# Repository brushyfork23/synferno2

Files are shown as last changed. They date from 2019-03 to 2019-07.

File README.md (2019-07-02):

# Synferno

Synferno is a flame-effect synchronizer which allows a DJ to easily trigger complex sequences of fireballs which perfectly match the music they’re playing.  The system consists of a console and four flame effects.  This codebase contains designs for building the console, the software which runs on it, and a the software for a flame-effect simulator to allow for bench testing.

## Physical Layout

The face of the console has 16 interface components:

 * One key-lock switch to ensure user is permitted to run console
 * One arming switch to ensure user wants to run console
 * Five white illuminated push-buttons to select sequence
 * Four red illuminated push-buttons for manually firing each of the four output channels individually
 * One large red illuminated push-button for manually firing all four output channels at once
 * One yellow illuminated push-button for resetting the down-beat and for flashing at the first beat of each stanza
 * One yellow illuminated push-button for manually tapping out a BPM and for flashing on each beat
 * One OLED screen which displays a menu
 * One rotary-encoder with integrated push-button for selecting and changing menu options

The back of the console has seven interface components:

 * One IEC power socket
 * One DIN-5 MIDI input port
 * Four SpeakOn connectors to deliver activation power to the four flame effects
 * One rocker-style power switch

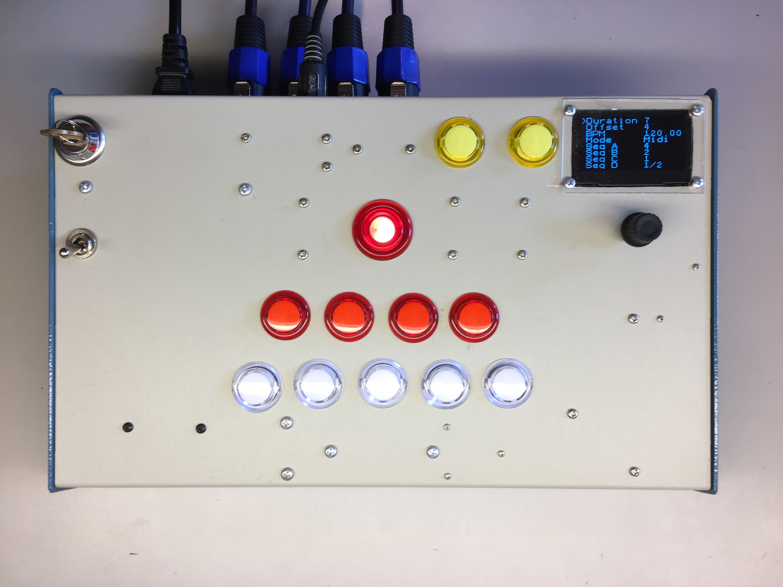
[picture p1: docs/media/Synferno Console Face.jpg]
Synferno Console Face


Included in `docs/diagrams/` are [renderings of each face and the positioning of internal components](docs/diagrams/Synferno2%20Console%20Interface%20Layout)

## Usage

The console’s primary function is to accept a BPM and energize the four SpeakOn output ports according to a selected sequence.  BPM can be read from a connected MIDI device or manually set by either tapping repeatedly on the Tap button or setting a value in the menu with the rotary encoder.  The beginning of a stanza (AKA the down-beat) can be set by pressing the Zero button.  A sequence is selected by toggling one of the five white buttons, and the sequence each button represents can be changed in the menu.  The duration of each activation is set in the menu.  Each output channel can be activated manually at any time by pressing the corresponding smaller red button, and all four channels may be triggered at once with the large red button.  There is a delay of several milliseconds between activation of an output port and the audible “POOF” from a flame effect, which can be compensated for by setting a delay in the menu.

## Testing

To bench test the console without connecting flame effects, the output ports can be connected to an adapter, which then connects to a computer running a flame-effect simulator.  The adaptor accepts 12V DC from the console via SpeakOn connectors, uses a four-channel optocoupler to convert their signals to 3.3V, reads those signals with an Arduino, and sends samples to the computer over a serial line.  The simulator running on the computer is a Processing application which looks for a positive signal coming from each channel then draws a rising ellipse and plays a POOF sound.

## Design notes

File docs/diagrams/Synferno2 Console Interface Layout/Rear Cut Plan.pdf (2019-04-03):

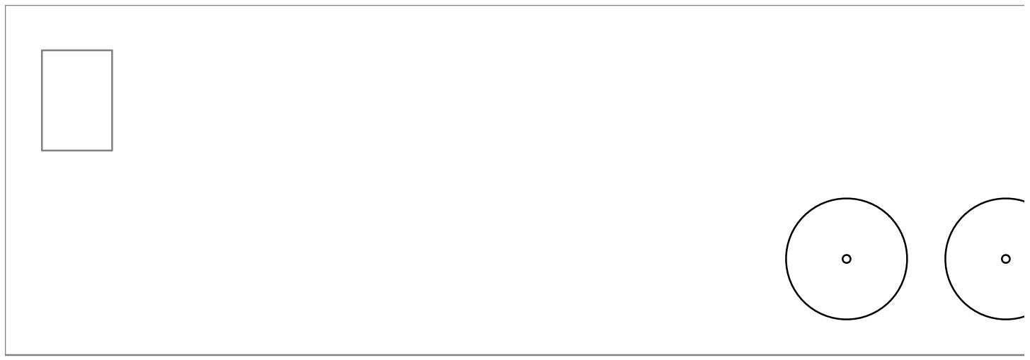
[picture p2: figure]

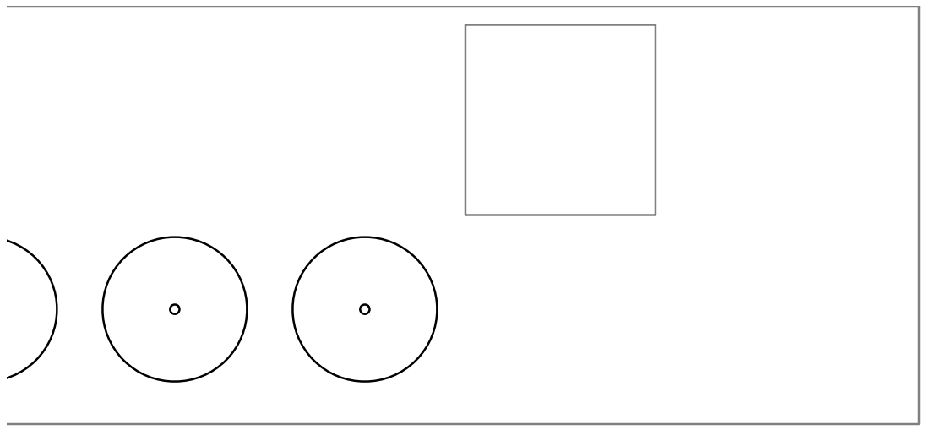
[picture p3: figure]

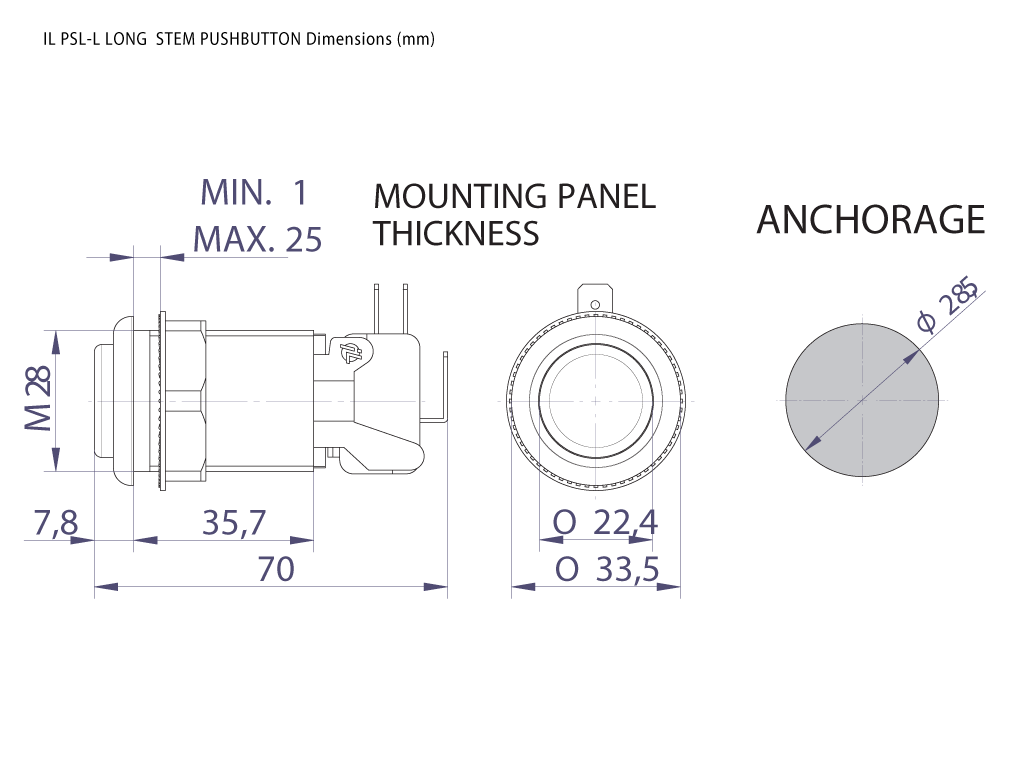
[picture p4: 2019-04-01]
docs/datasheets/il_PSLL_A0211_spec__46602.1422125104.1280.1280.png

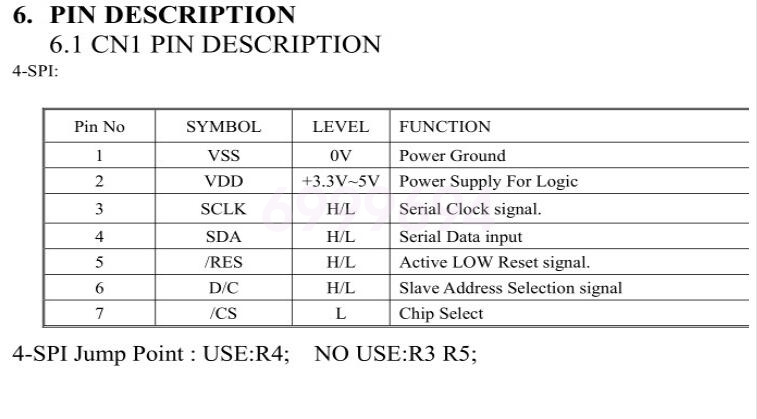
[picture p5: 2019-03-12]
docs/datasheets/OLED 5.jpg

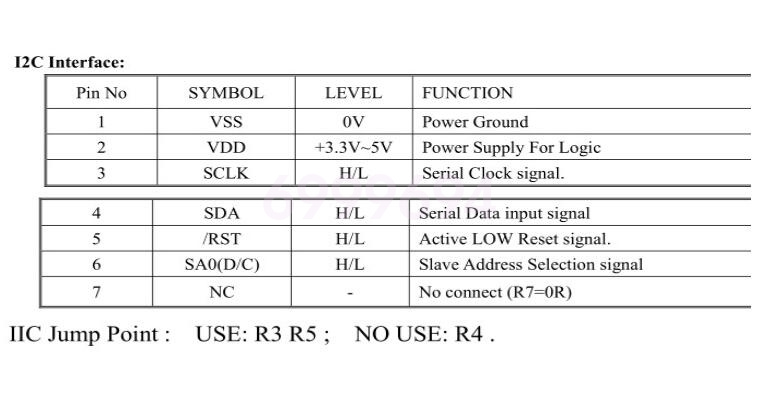
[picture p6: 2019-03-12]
docs/datasheets/OLED 6.jpg

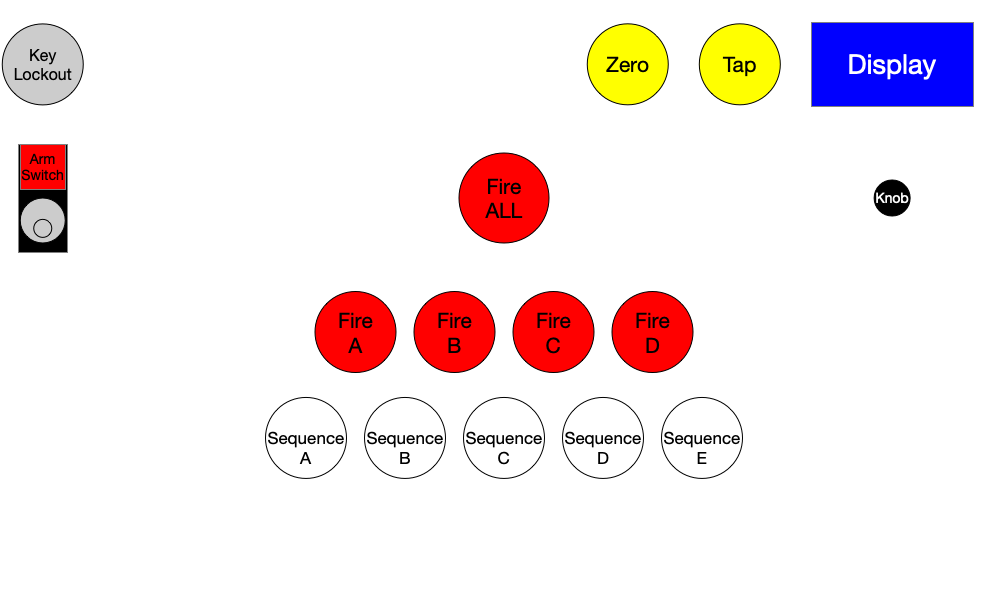
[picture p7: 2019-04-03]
docs/diagrams/Synferno2 Console Interface Layout/Birds Eye.png

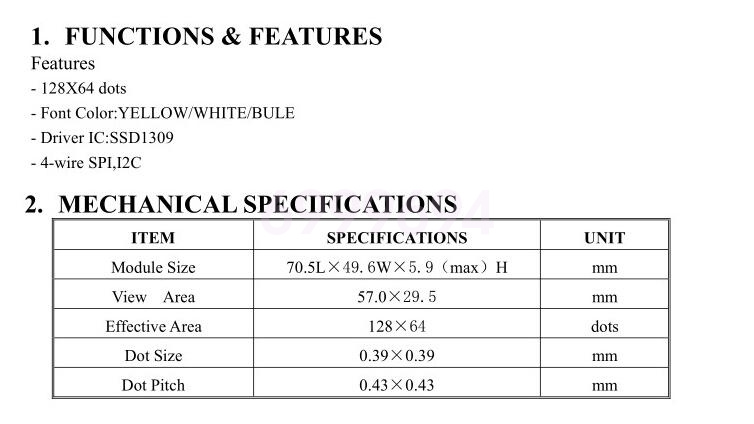
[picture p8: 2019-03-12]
docs/datasheets/OLED 2.jpg

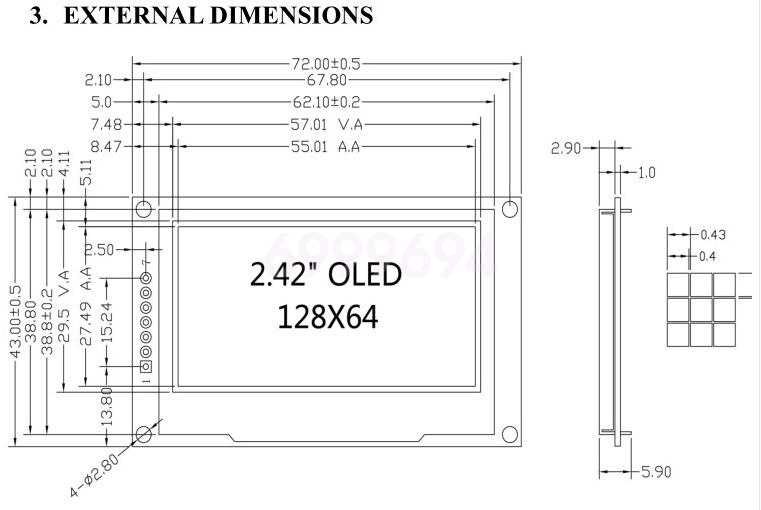
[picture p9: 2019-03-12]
docs/datasheets/OLED 3.jpg

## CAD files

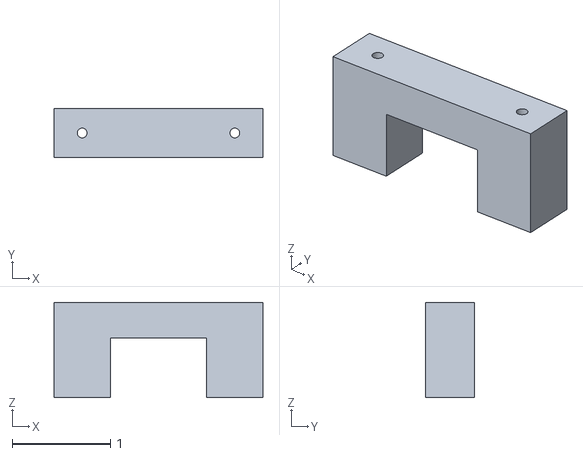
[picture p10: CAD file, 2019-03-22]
models/PSU Stop.stl
2.12 x 0.5 x 0.965

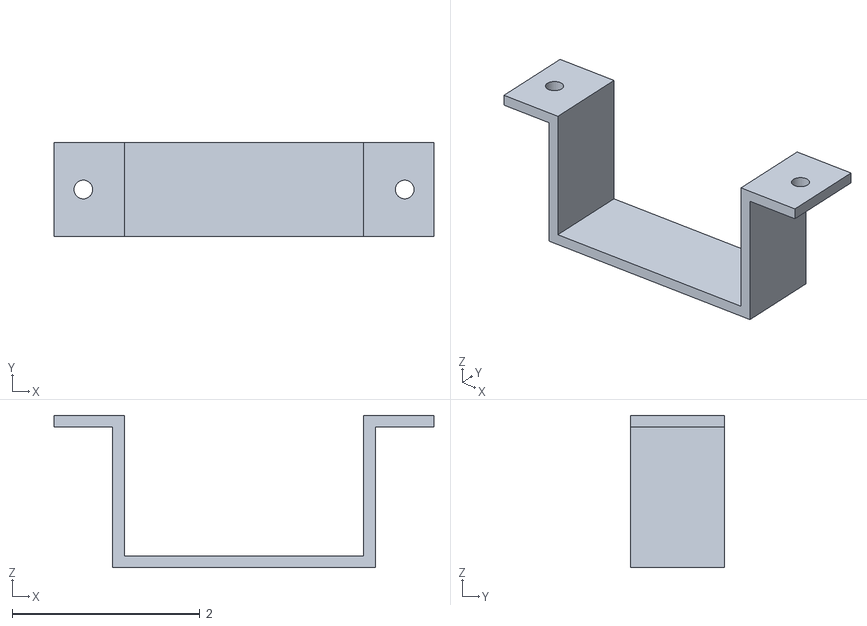
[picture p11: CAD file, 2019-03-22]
models/PSU BRKT.stl
4.05 x 1.00 x 1.62

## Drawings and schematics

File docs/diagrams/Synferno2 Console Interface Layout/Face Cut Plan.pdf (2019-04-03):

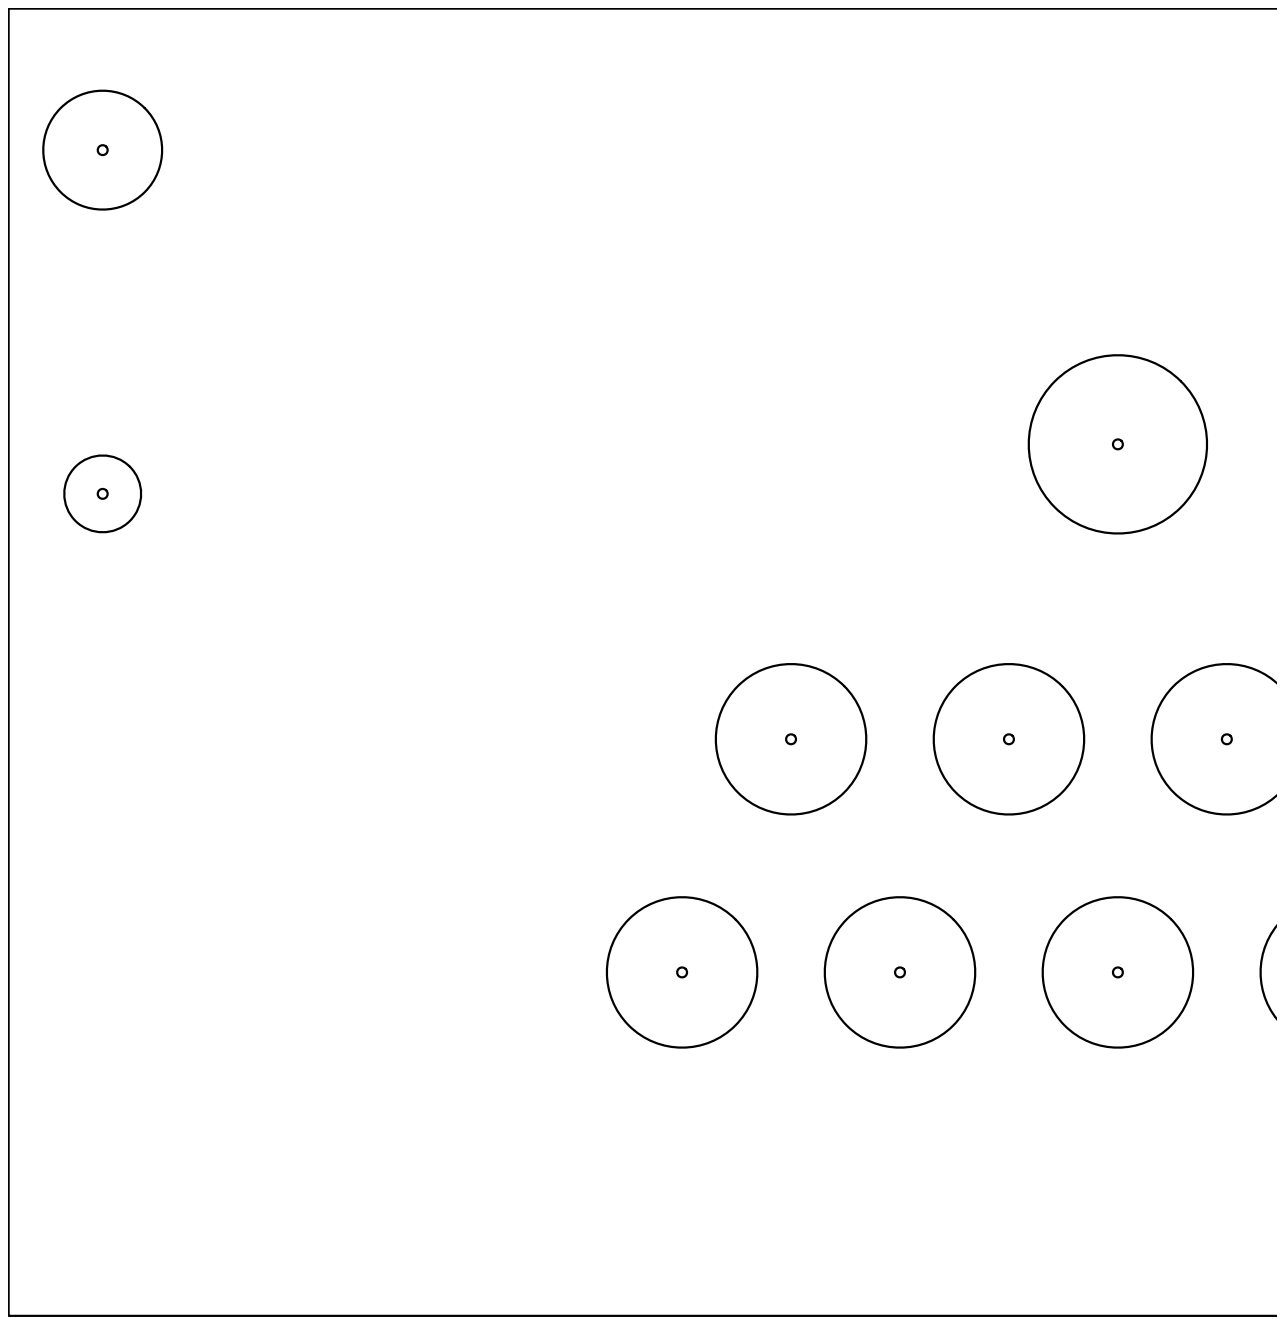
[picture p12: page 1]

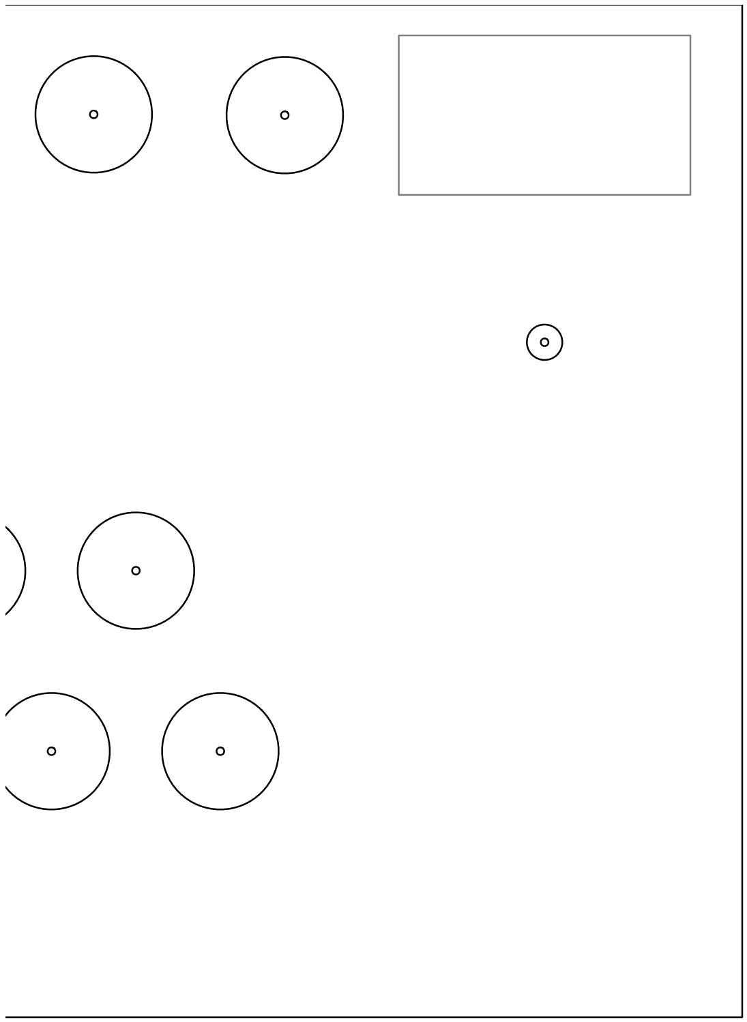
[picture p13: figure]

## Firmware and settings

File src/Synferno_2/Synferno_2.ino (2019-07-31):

//TODO: add a menu option to set the minimum sequence priority we will render.
// It'd be like simulating degredation, but would be used for fuel saving.

// Compile for Arduino Mega 2560

// Arduino Mega 2560: https://smile.amazon.com/Elegoo-EL-CB-003-ATmega2560-ATMEGA16U2-Arduino/dp/B01H4ZLZLQ
// WEMOS LOLIN D1 mini: https://wiki.wemos.cc/products:d1:d1_mini
// Blue 2.42" SSD1309 128x64 OLED: https://www.ebay.com/itm/253714699654
// Rotary Encoder w/ Click switch: https://www.ebay.com/itm/232396602079
// MIDI Breakout Board: https://smile.amazon.com/gp/product/B00YDLVLVO
// IRF520 MOSFET Driver Module: https://smile.amazon.com/gp/product/B06XHH1TQM
// 12V / 5V DC Buck Converter: https://smile.amazon.com/gp/product/B01MEESLZ6
// 12V 10A Power Supply: https://smile.amazon.com/gp/product/B00Z9X4GLW

// Arduino Mega
// A2 to OLED `CS`
// A8 to Rotary Encoder `CLK`
// A10 to Rotary Encoder `DT`
// 2 to Pushbutton Fire 0 `LED`
// 3 to Pushbutton Fire 1 `LED`
// 4 to Pushbutton Fire 2 `LED`
// 5 to Pushbutton Fire 3 `LED`
// 6 to Pushbutton Zero `LED`
// 7 to Pushbutton Freq 0 `LED`
// 8 to Pushbutton Freq 1 `LED`
// 9 to Pushbutton Freq 2 `LED`
// 10 to Pushbutton Freq 3 `LED`
// 11 to Pushbutton Freq 4 `LED`
// 12 to Pushbutton Tap `LED`
// 16 to MIDI `tx`
// 17 to MIDI `rx`
// 18 to ESP8266 `RX`
// 19 to ESP8266 `TX`
// 20 to OLED `SDA`
// 21 to OLED `SCLK`
// 22 to OLED `DC`
// 23 to OLED `RES`
// 24 to Rotary Encoder `SW`
// 25 to MOSFET Driver Module 0 `SIG`
// 26 to MOSFET Driver Module 1 `SIG`
// 27 to MOSFET Driver Module 2 `SIG`
// 28 to MOSFET Driver Module 3 `SIG`
// 29 to Pushbutton Freq 0 `signal`
// 30 to Pushbutton Freq 1 `signal`
// 31 to Pushbutton Freq 2 `signal`
// 32 to Pushbutton Freq 3 `signal`
// 33 to Pushbutton Freq 4 `signal`
// 34 to Pushbutton Fire 0 `signal`
// 35 to Pushbutton Fire 1 `signal`
// 36 to Pushbutton Fire All `signal`
// 37 to Pushbutton Fire 2 `signal`
// 38 to Pushbutton Fire 3 `signal`
// 39 to Pushbutton Zero `signal`
// 40 to Pushbutton Tap `signal`

// Is this actually necessary?
// The mega should be getting its power from the 12v through the barrel jack
// and all the 5v components should be powered from the buck converter.
// This would be taking the regulated +5 on the mega and piping it into
// the `+5` rail, and we probably don't want other components pulling off the mega for power.
// VCC to Buck Converter `+5`

// GND to GND

// WEMOS LOLIN D1 mini (ESP8266)
// TX to Mega 19 (`RX1`)
// RX to Mega 18 (`TX1`)
// 5V to Buck Converter `+5`
// GND to GND

// SSD1309 OLED
// CS to Mega A2
// DC to Mega 22
// RES to Mega 23
// SDA to Mega 20
// SCLK to Mega 21
// VDD to Buck Converter `+5`
// VSS to GND

// Click Encoder
// CLK to Mega A8
// DT to Mega A10
// SW to Mega 24
// + to Buck Converter `+5`
// GND to GND

// MOSFET Driver Module (0)
// SIG to Mega 25
// VCC to Buck Converter `+5`
// GND to GND

// MOSFET Driver Module (1)
// SIG to Mega 26
// VCC to Buck Converter `+5`
// GND to GND

// MOSFET Driver Module (2)
// SIG to Mega 27
// VCC to Buck Converter `+5`
// GND to GND

// MOSFET Driver Module (3)
// SIG to Mega 28
// VCC to Buck Converter `+5`
// GND to GND

// Midi breakout
// tx to Mega 16 (`RX2`)
// rx to Mega 17 (`TX2`)
// + to Buck Converter `+5`
// - to GND

// Required libraries
// ArduinoStreaming: https://github.com/geneReeves/ArduinoStreaming
// Metro: https://github.com/thomasfredericks/Metro-Arduino-Wiring
// Bounce2: https://github.com/thomasfredericks/Bounce2
// ArduinoMenu_library: https://github.com/neu-rah/ArduinoMenu
// > encoder: https://github.com/christophepersoz/encoder
// U8g2: https://github.com/olikraus/U8g2_Arduino

#include <Streaming.h>
#include <Metro.h>

// MIDI
#include "MIDI.h"
MIDI midi;

// ManualBeat
#include "ManualBeat.h"
ManualBeat manualBeat;

// Solenoids
#include "Solenoid.h"
Solenoid fireA, fireB, fireC, fireD;

// Push buttons
#include "Button.h"
#define BRIGHTNESS_BRIGHT_RED 230
#define BRIGHTNESS_DIM_RED 20
#define BRIGHTNESS_BRIGHT_YELLOW 255
#define BRIGHTNESS_DIM_YELLOW 30
#define BTN_FIRE_0_PIN 34
#define BTN_FIRE_1_PIN 35
#define BTN_FIRE_2_PIN 37
#define BTN_FIRE_3_PIN 38
#define BTN_FIRE_ALL_PIN 36
#define BTN_ZERO_PIN 39
#define BTN_TAP_PIN 40
#define LED_FIRE_0_PIN 2
#define LED_FIRE_1_PIN 3
#define LED_FIRE_2_PIN 4
#define LED_FIRE_3_PIN 5
#define LED_ZERO_PIN 6
#define LED_TAP_PIN 12
Button fireAllNow;
Button fireANow;
Button fireBNow;
Button fireCNow;
Button fireDNow;
Button zero;
Button tap;

// Sequence buttons
#include "ButtonGroup.h"
#define NUM_SEQUENCE_BUTTONS 5
#define SEQUENCE_SCALE 4
byte SEQUENCE_BUTTON_PINS[NUM_SEQUENCE_BUTTONS] = {29, 30, 31, 32, 33};
byte SEQUENCE_LED_PINS[NUM_SEQUENCE_BUTTONS] = {7, 8, 9, 10, 11};
ButtonGroup sequenceButtons;

// Sequences
#include "sequences.h";
struct Sequence *activeSequence;

// Fire Marshal
#include "FireMarshal.h"
FireMarshal fireMarshal;

/*
 * Begin Menu
 */
#include <menu.h>
#include <menuIO/U8x8Out.h>
#include <menuIO/keyIn.h>
#include <SPI.h>
using namespace Menu;
#define ENC_CLK    A8
#define ENC_DT    A10
#define ENC_BTN  24
#define OLED_CS A2
#define OLED_DC 22
#define OLED_RST 23
#define USE_HWI2C
U8X8_SSD1309_128X64_NONAME0_4W_SW_SPI u8x8(SCL, SDA, OLED_CS, OLED_DC, OLED_RST);

#define MODE_MIDI 0
#define MODE_MANUAL 1
boolean hasConfigChange = false;
int longDuration=7; // Number of clock ticks per beat to fire for a big poof
int shortDuration=4; // Number of clock ticks per beat to fire for a little poof
float bpm=120.0;
int offset=0; // Number of clock ticks early to trigger the next beat
int mode=MODE_MIDI;
enum priorityRangeMenuOption : uint8_t {
  PRIORITY_RANGE_ANY = 0,
  PRIORITY_RANGE_GT_LOW,
  PRIORITY_RANGE_LOW,
  PRIORITY_RANGE_MEDIUM,
  PRIORITY_RANGE_HIGH
};
uint8_t priorityRangeSelection=PRIORITY_RANGE_ANY;

struct Sequence *seqAPtr = &sequence_cbda_400;
struct Sequence *seqBPtr = &sequence_cbda_200;
struct Sequence *seqCPtr = &sequence_cbda_100;
struct Sequence *seqDPtr = &sequence_cbda_050;
struct Sequence *seqEPtr = &sequence_cbda_025;

result selectMidi();
result selectManual();
result configUpdate() {
  hasConfigChange = true;
  return proceed;
}
result onBPMMenuUpdate() {
  manualBeat.setBPM(bpm);
  setBpm(bpm);
  return configUpdate();
}

result onLongDurationMenuUpdate() {
  fireMarshal.setLongDuration(longDuration);
  updateSequenceDegredation();
  return configUpdate();
}

result onShortDurationMenuUpdate() {
  fireMarshal.setShortDuration(shortDuration);
  updateSequenceDegredation();
  return configUpdate();
}

TOGGLE(mode,modeMenu,"Mode     ",Menu::doNothing,Menu::noEvent,Menu::noStyle
  ,VALUE("Midi",MODE_MIDI,selectMidi,Menu::noEvent)
  ,VALUE("Manual",MODE_MANUAL,selectManual,Menu::noEvent)
);

SELECT(priorityRangeSelection,priorityRangeMenu,"Pri    ",configUpdate,Menu::exitEvent,Menu::noStyle
  ,VALUE("Any",PRIORITY_RANGE_ANY,Menu::doNothing,Menu::noEvent)
  ,VALUE(">= Med",PRIORITY_RANGE_GT_LOW,Menu::doNothing,Menu::noEvent)
  ,VALUE("Low",PRIORITY_RANGE_LOW,Menu::doNothing,Menu::noEvent)
  ,VALUE("Medium",PRIORITY_RANGE_MEDIUM,Menu::doNothing,Menu::noEvent)
  ,VALUE("High",PRIORITY_RANGE_HIGH,Menu::doNothing,Menu::noEvent)
);

SELECT(seqAPtr,seqAMenu,"Seq1",configUpdate,Menu::exitEvent,Menu::noStyle
  ,VALUE(SEQUENCE_TITLE_CBDA_400,&sequence_cbda_400,Menu::doNothing,Menu::noEvent)
  ,VALUE(SEQUENCE_TITLE_CBDA_200,&sequence_cbda_200,Menu::doNothing,Menu::noEvent)
  ,VALUE(SEQUENCE_TITLE_CBDA_100,&sequence_cbda_100,Menu::doNothing,Menu::noEvent)
  ,VALUE(SEQUENCE_TITLE_CBDA_050,&sequence_cbda_050,Menu::doNothing,Menu::noEvent)
  ,VALUE(SEQUENCE_TITLE_CBDA_025,&sequence_cbda_025,Menu::doNothing,Menu::noEvent)
  ,VALUE(SEQUENCE_TITLE_A_B_C_D_050,&sequence_a_b_c_d_050,Menu::doNothing,Menu::noEvent)
  ,VALUE(SEQUENCE_TITLE_D_C_B_A_050,&sequence_d_c_b_a_050,Menu::doNothing,Menu::noEvent)
  ,VALUE(SEQUENCE_TITLE_DNB,&sequence_dnb,Menu::doNothing,Menu::noEvent)
);

SELECT(seqBPtr,seqBMenu,"Seq2",configUpdate,Menu::exitEvent,Menu::noStyle
  ,VALUE(SEQUENCE_TITLE_CBDA_400,&sequence_cbda_400,Menu::doNothing,Menu::noEvent)
  ,VALUE(SEQUENCE_TITLE_CBDA_200,&sequence_cbda_200,Menu::doNothing,Menu::noEvent)
  ,VALUE(SEQUENCE_TITLE_CBDA_100,&sequence_cbda_100,Menu::doNothing,Menu::noEvent)
  ,VALUE(SEQUENCE_TITLE_CBDA_050,&sequence_cbda_050,Menu::doNothing,Menu::noEvent)
  ,VALUE(SEQUENCE_TITLE_CBDA_025,&sequence_cbda_025,Menu::doNothing,Menu::noEvent)
  ,VALUE(SEQUENCE_TITLE_A_B_C_D_050,&sequence_a_b_c_d_050,Menu::doNothing,Menu::noEvent)
  ,VALUE(SEQUENCE_TITLE_D_C_B_A_050,&sequence_d_c_b_a_050,Menu::doNothing,Menu::noEvent)
  ,VALUE(SEQUENCE_TITLE_DNB,&sequence_dnb,Menu::doNothing,Menu::noEvent)
);

SELECT(seqCPtr,seqCMenu,"Seq3",configUpdate,Menu::exitEvent,Menu::noStyle
  ,VALUE(SEQUENCE_TITLE_CBDA_400,&sequence_cbda_400,Menu::doNothing,Menu::noEvent)
  ,VALUE(SEQUENCE_TITLE_CBDA_200,&sequence_cbda_200,Menu::doNothing,Menu::noEvent)
  ,VALUE(SEQUENCE_TITLE_CBDA_100,&sequence_cbda_100,Menu::doNothing,Menu::noEvent)
  ,VALUE(SEQUENCE_TITLE_CBDA_050,&sequence_cbda_050,Menu::doNothing,Menu::noEvent)
  ,VALUE(SEQUENCE_TITLE_CBDA_025,&sequence_cbda_025,Menu::doNothing,Menu::noEvent)
  ,VALUE(SEQUENCE_TITLE_A_B_C_D_050,&sequence_a_b_c_d_050,Menu::doNothing,Menu::noEvent)
  ,VALUE(SEQUENCE_TITLE_D_C_B_A_050,&sequence_d_c_b_a_050,Menu::doNothing,Menu::noEvent)
  ,VALUE(SEQUENCE_TITLE_DNB,&sequence_dnb,Menu::doNothing,Menu::noEvent)
);

SELECT(seqDPtr,seqDMenu,"Seq4",configUpdate,Menu::exitEvent,Menu::noStyle
  ,VALUE(SEQUENCE_TITLE_CBDA_400,&sequence_cbda_400,Menu::doNothing,Menu::noEvent)
  ,VALUE(SEQUENCE_TITLE_CBDA_200,&sequence_cbda_200,Menu::doNothing,Menu::noEvent)
  ,VALUE(SEQUENCE_TITLE_CBDA_100,&sequence_cbda_100,Menu::doNothing,Menu::noEvent)
  ,VALUE(SEQUENCE_TITLE_CBDA_050,&sequence_cbda_050,Menu::doNothing,Menu::noEvent)
  ,VALUE(SEQUENCE_TITLE_CBDA_025,&sequence_cbda_025,Menu::doNothing,Menu::noEvent)
  ,VALUE(SEQUENCE_TITLE_A_B_C_D_050,&sequence_a_b_c_d_050,Menu::doNothing,Menu::noEvent)
  ,VALUE(SEQUENCE_TITLE_D_C_B_A_050,&sequence_d_c_b_a_050,Menu::doNothing,Menu::noEvent)
  ,VALUE(SEQUENCE_TITLE_DNB,&sequence_dnb,Menu::doNothing,Menu::noEvent)
);

SELECT(seqEPtr,seqEMenu,"Seq5",configUpdate,Menu::exitEvent,Menu::noStyle
  ,VALUE(SEQUENCE_TITLE_CBDA_400,&sequence_cbda_400,Menu::doNothing,Menu::noEvent)
  ,VALUE(SEQUENCE_TITLE_CBDA_200,&sequence_cbda_200,Menu::doNothing,Menu::noEvent)
  ,VALUE(SEQUENCE_TITLE_CBDA_100,&sequence_cbda_100,Menu::doNothing,Menu::noEvent)
  ,VALUE(SEQUENCE_TITLE_CBDA_050,&sequence_cbda_050,Menu::doNothing,Menu::noEvent)
  ,VALUE(SEQUENCE_TITLE_CBDA_025,&sequence_cbda_025,Menu::doNothing,Menu::noEvent)
  ,VALUE(SEQUENCE_TITLE_A_B_C_D_050,&sequence_a_b_c_d_050,Menu::doNothing,Menu::noEvent)
  ,VALUE(SEQUENCE_TITLE_D_C_B_A_050,&sequence_d_c_b_a_050,Menu::doNothing,Menu::noEvent)
  ,VALUE(SEQUENCE_TITLE_DNB,&sequence_dnb,Menu::doNothing,Menu::noEvent)
);

MENU(mainMenu,"   SYNFERNO",Menu::doNothing,Menu::noEvent,Menu::noStyle
  ,FIELD(bpm,"BPM     ","",0.0,300.0,1.0,0.1,onBPMMenuUpdate,Menu::exitEvent,Menu::noStyle)
  ,FIELD(offset,"Offset  ","",0,23,1,0,configUpdate,Menu::exitEvent,Menu::wrapStyle)
  ,FIELD(longDuration,"Big poof","",1,23,1,0,onLongDurationMenuUpdate,Menu::exitEvent,Menu::noStyle)
  ,FIELD(shortDuration,"Lil poof","",1,23,1,0,onShortDurationMenuUpdate,Menu::exitEvent,Menu::noStyle)
  ,SUBMENU(priorityRangeMenu)
  ,SUBMENU(modeMenu)
  ,SUBMENU(seqAMenu)
  ,SUBMENU(seqBMenu)
  ,SUBMENU(seqCMenu)
  ,SUBMENU(seqDMenu)
  ,SUBMENU(seqEMenu)
);

#define MAX_DEPTH 2

result selectMidi() {
  // Disable manual BPM setting
  mainMenu[0].enabled=disabledStatus;
  fireMarshal.clear();
  return configUpdate();
}

result selectManual() {
  // Enable manual BPM setting
  mainMenu[0].enabled=enabledStatus;
  manualBeat.resetCounter();
  if (bpm == 0.0) {
    setBpm(120.0);
  }
  fireMarshal.clear();
  return configUpdate();
}

//#include <menuIO/clickEncoderIn.h>
#include "clickEncoderIn.h"
ClickEncoder clickEncoder(ENC_CLK, ENC_DT, ENC_BTN, LOW);
ClickEncoderStream encStream(clickEncoder,1);

MENU_OUTPUTS(out,MAX_DEPTH
  ,U8X8_OUT(u8x8,{0,0,16,8})
  ,NONE
);
  
NAVROOT(nav,mainMenu,MAX_DEPTH,encStream,out);
/**
 * End MENU
 */


// Local variables
long inNum = 0;
char inCommand;

void setup() {
  Serial.begin(115200);
  while(!Serial);

  Serial1.begin(115200);
  while(!Serial1);

  // fire up the Screen
  SPI.begin();
  u8x8.begin();
  /*
  u8x8_font_artossans8_r
  u8x8_font_victoriamedium8_r
  u8x8_font_pxplusibmcgathin_f
  u8x8_font_pxplusibmcga_f
  u8x8_font_pressstart2p_f
  u8x8_font_pxplustandynewtv_f
  */
  u8x8.setFont(u8x8_font_artossans8_r);

  // load up the sequences
  Sequences::init();

  // this sequence is not actually active, but this way updates to the "current sequence" don't attempt to set null values
  activeSequence = seqAPtr;

  // configure Menu
  nav.showTitle=false;
  mainMenu[0].enabled=disabledStatus;

  // fire up MIDI
  midi.begin();

  // fire up the fire
  fireA.begin(SOLENOID_PIN0);
  fireB.begin(SOLENOID_PIN1);
  fireC.begin(SOLENOID_PIN2);
  fireD.begin(SOLENOID_PIN3);

  // buttons
  // make fire now
  fireAllNow.begin(BTN_FIRE_ALL_PIN);
  fireANow.begin(BTN_FIRE_0_PIN);
  analogWrite(LED_FIRE_0_PIN, BRIGHTNESS_DIM_RED);
  pinMode(LED_FIRE_0_PIN, OUTPUT);
  fireBNow.begin(BTN_FIRE_1_PIN);
  analogWrite(LED_FIRE_1_PIN, BRIGHTNESS_DIM_RED);
  pinMode(LED_FIRE_1_PIN, OUTPUT);
  fireCNow.begin(BTN_FIRE_2_PIN);
  analogWrite(LED_FIRE_2_PIN, BRIGHTNESS_DIM_RED);
  pinMode(LED_FIRE_2_PIN, OUTPUT);
  fireDNow.begin(BTN_FIRE_3_PIN);
  analogWrite(LED_FIRE_3_PIN, BRIGHTNESS_DIM_RED);
  pinMode(LED_FIRE_3_PIN, OUTPUT);
  // reset midi counter to zero
  zero.begin(BTN_ZERO_PIN);
  analogWrite(LED_ZERO_PIN, BRIGHTNESS_DIM_YELLOW);
  pinMode(LED_ZERO_PIN, OUTPUT);
  // tap bpm
  tap.begin(BTN_TAP_PIN);
  analogWrite(LED_TAP_PIN, BRIGHTNESS_DIM_YELLOW);
  pinMode(LED_TAP_PIN, OUTPUT);
  manualBeat.setBPM(bpm);
  // sequences of poofs
  sequenceButtons.begin(NUM_SEQUENCE_BUTTONS, SEQUENCE_BUTTON_PINS, SEQUENCE_LED_PINS);

  // fire up the fire marshal
  fireMarshal.setLongDuration(longDuration);
  fireMarshal.setShortDuration(shortDuration);
}

void loop() {
  // 0. handle rotary encoder menu
  static Metro encoderUpdate(1UL);
  if (encoderUpdate.check()) {
    clickEncoder.service();
    encoderUpdate.reset();
  }
  static Metro navInterval(1UL);
  if (navInterval.check()) {
    navInterval.reset();
    nav.poll();
  }
  
  // 1. handle web portal
  // send updates
  if (hasConfigChange) {
    hasConfigChange = false;
    sendToWebserver();
  }
  // fetch updates
  handleWebserverUpdates();
  
  // 2. handle tap button
  if (mode == MODE_MANUAL) {
    if (tap.update() && tap.getState()) {
      handleTap();
    }
  }

  // 3. handle sequence selection button group
  if ( sequenceButtons.update() ) {
    if ( !sequenceButtons.hasSelection() ) {
      fireMarshal.clear();
    } else {
      switch (sequenceButtons.getValue()) {
        case 0:
          activeSequence = seqAPtr;
          break;
        case 1:
          activeSequence = seqBPtr;
          break;
        case 2:
          activeSequence = seqCPtr;
          break;
        case 3:
          activeSequence = seqDPtr;
          break;
        case 4:
          activeSequence = seqEPtr;
          break;
      }
      updateSequenceDegredation();
    }
  }
  
  // 4. handle zero button
  // If the zero button is momentarily pressed, reset the clock counters. This marks the beginning of a bar.
  if (zero.update()) {
    togglePWMLED(zero.getState(), LED_ZERO_PIN, BRIGHTNESS_BRIGHT_YELLOW, BRIGHTNESS_DIM_YELLOW);
    if (zero.getState()) {
      resetClockCounter();
    }
  }

  // 5. handle beat
  // if we have no beat (manual or MIDI), shut it down.
  if (getClockCounter()==255) {
    fireMarshal.clear();
  }
  // if we have a clock tick, update the firing status and beat indicators.
  if( updateClockCounter() ) {
    handleBeat();
  }

  // 6. Handle poofers.
  // provide the fire marshal with the most up-to-date button and counter states
  fireAllNow.update();
  fireANow.update();
  fireBNow.update();
  fireCNow.update();
  fireDNow.update();
  fireMarshal.setManualAll(fireAllNow.getState());
  fireMarshal.setManualA(fireANow.getState());
  fireMarshal.setManualB(fireBNow.getState());
  fireMarshal.setManualC(fireCNow.getState());
  fireMarshal.setManualD(fireDNow.getState());
  // process all the states and determine firing status
  fireMarshal.update();
  // actually turn the poofers on or off, based on the determination of the fire marshal
  if (fireMarshal.getFireStateA()) {
    if (!fireA.getState()) {
        fireA.on();
    }
  } else {
      if (fireA.getState()) {
          fireA.off();
      }
  }
  if (fireMarshal.getFireStateB()) {
      if (!fireB.getState()) {
          fireB.on();
      }
  } else {
      if (fireB.getState()) {
          fireB.off();
      }
  }
  if (fireMarshal.getFireStateC()) {
      if (!fireC.getState()) {
          fireC.on();
      }
  } else {
      if (fireC.getState()) {
          fireC.off();
      }
  }
  if (fireMarshal.getFireStateD()) {
      if (!fireD.getState()) {
          fireD.on();
      }
  } else {
      if (fireD.getState()) {
          fireD.off();
      }
  }
        
  
  // 7. handle fire indicators
  // Report changes in firing status (change in solenoid state) by lighting the fire-now buttons.
  if ( fireA.update() ) {
    togglePWMLED(fireA.getState(), LED_FIRE_0_PIN, BRIGHTNESS_BRIGHT_RED, BRIGHTNESS_DIM_RED);
  }
  if ( fireB.update() ) {
    togglePWMLED(fireB.getState(), LED_FIRE_1_PIN, BRIGHTNESS_BRIGHT_RED, BRIGHTNESS_DIM_RED);
  }
  if ( fireC.update() ) {
    togglePWMLED(fireC.getState(), LED_FIRE_2_PIN, BRIGHTNESS_BRIGHT_RED, BRIGHTNESS_DIM_RED);
  }
  if ( fireD.update() ) {
    togglePWMLED(fireD.getState(), LED_FIRE_3_PIN, BRIGHTNESS_BRIGHT_RED, BRIGHTNESS_DIM_RED);
  }

  // MISC. code for debugging, reporting, etc. to the Serial line

  // We need CLOCK_TICKS_PER_BEAT updates per beat, so minimum updates per second is:
  static word updateFloor = CLOCK_TICKS_PER_BEAT * 200 / 60;

  // track updates per second.
  static unsigned long counter = 0;
  counter ++;
  static Metro updateInterval(1000UL);
  if ( updateInterval.check() ) {
    //Serial << F("Updates per second: ") << counter << endl;
    if ( counter < updateFloor ) Serial << F("CAUTION: loop() < updateFloor!!") << endl;
    counter = 0;
    updateInterval.reset();
  }
}

boolean updateClockCounter() {
  boolean hasMidiUpdate = midi.update();
  boolean hasManualUpdate = manualBeat.update();
  if (mode == MODE_MIDI) {
    setBpm(midi.getBPM());
    return hasMidiUpdate;
  } else {
    return hasManualUpdate;
  }
}

void setBpm(float val) {
  // set the new global value
  bpm = val;
  if (bpm > 0) {
    // update sequence priority support level
    updateSequenceDegredation();
  }
}

// determine what priority level we can support for the given bpm, duration, and sequence.
void updateSequenceDegredation() {
  activeSequence->updateViablePriority(minimumTicksBetweenLongPoofTrigger(), minimumTicksBetweenShortPoofTrigger());
}

// determine firing time and display beat information.
void handleBeat() {
  byte counter = getClockCounter();

  // report beat
  showBeat((counter + offset) % CLOCK_TICKS_PER_BEAT);

  // report bar beginning
  if (!zero.getState()){
    showBar( (counter + offset) % (CLOCK_TICKS_PER_BEAT * SCALE));
  }

  // how far back from the beat do we need to trigger each poofer?
  if (!sequenceButtons.hasSelection()) {
    fireMarshal.clear();
  } else {
    trigger_priority priorityMin, priorityMax;
    switch(priorityRangeSelection) {
      case PRIORITY_RANGE_ANY:
        priorityMin = PRIORITY_LOW;
        priorityMax = PRIORITY_HIGH;
        break;
      case PRIORITY_RANGE_GT_LOW:
        priorityMin = PRIORITY_MEDIUM;
        priorityMax = PRIORITY_HIGH;
        break;
      case PRIORITY_RANGE_LOW:
        priorityMin = PRIORITY_LOW;
        priorityMax = PRIORITY_LOW;
        break;
      case PRIORITY_RANGE_MEDIUM:
        priorityMin = PRIORITY_MEDIUM;
        priorityMax = PRIORITY_MEDIUM;
        break;
      case PRIORITY_RANGE_HIGH:
        priorityMin = PRIORITY_HIGH;
        priorityMax = PRIORITY_HIGH;
        break;
    }
    TickTriggers triggers = activeSequence->getTickTriggers((counter + offset) % (CLOCK_TICKS_PER_BEAT * SCALE), priorityMin, priorityMax);
    fireMarshal.setSequenceTriggers(triggers.poofSizeA, triggers.poofSizeB, triggers.poofSizeC, triggers.poofSizeD);
  }

  fireMarshal.tickBeatCounter();
}

// helper function to work through the modulo-24 stuff.  PITA.
boolean timeForFire( byte clock, byte start, byte stop ) {
  // edge case
  if( start == stop ) return( false );

  // easy case.
  if( stop > start ) {
    if( clock >= start && clock < stop ) return( true );
    else return( false );
  }

  // so, start > stop
  // harder case, with the modulo-24 stuff.  Ugh.
  if( clock >= stop && clock < start ) return( false );
  else return( true );
  
}

/*
  Compute the number of ticks required to perform a large poof.

  The minimum ticks between triggers is
  ceil(millisPerTrigger / millisPerTick)

  millisPerTrigger is (duration * millisPerTick) + lockout window

  Fully expanded, minimum ticks between triggers would be:
  duration * ((MILLIS_PER_MINUTE / bpm) / CLOCK_TICKS_PER_BEAT) + 200UL
                                /
        ((MILLIS_PER_MINUTE / bpm) / CLOCK_TICKS_PER_BEAT)
  
 */
uint8_t minimumTicksBetweenLongPoofTrigger() {
  int millisPerBeat = MILLIS_PER_MINUTE / bpm;
  int millisPerTick = millisPerBeat / CLOCK_TICKS_PER_BEAT;

  return ceil(longDuration + (200UL / millisPerTick));
}

// Compute the number of ticks required to perform a small poof.
uint8_t minimumTicksBetweenShortPoofTrigger() {
  int millisPerBeat = MILLIS_PER_MINUTE / bpm;
  int millisPerTick = millisPerBeat / CLOCK_TICKS_PER_BEAT;

  return ceil(shortDuration + (200UL / millisPerTick));
}
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

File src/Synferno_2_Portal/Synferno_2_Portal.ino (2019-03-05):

// Compile for Lolin D1 mini V3.1.0 ESP8266

// WEMOS LOLIN D1 mini (ESP8266)
// TX to Mega 19 (`RX1`)
// RX to Mega 18 (`TX1`)
// 5V to Buck Converter `+5`
// GND to GND

#define AP_SSID "synferno"
#define AP_PASS "password"
#define HOSTNAME "synferno"
#define LOCAL_IP 192,168,4,22
#define GATEWAY 192,168,4,9
#define SUBNET 255,255,255,0
#define WWW_USER "admin"
#define WWW_PASS "password"
#define MAX_OFFSET 24
#define MAX_BPM 300
#define MAX_DURATION 24

//#include <WiFi.h>
#include <ESP8266WiFi.h>
#include <WiFiClient.h>
#include <ESP8266WebServer.h>
#include <ESP8266mDNS.h>

ESP8266WebServer server(80);

long inNum = 0;    // int to hold Serial input
char inCommand;

int duration=2;
int bpm=120;
int offset=0;
int mode=0;


//Check if header is present and correct
boolean is_authenticated() {
  if (server.hasHeader("Cookie")) {
    String cookie = server.header("Cookie");
    if (cookie.indexOf("ESPSESSIONID=1") != -1) {
      return true;
    }
  }
  return false;
}

//login page, also called for disconnect
void handleLogin() {
  String msg;
  if (server.hasArg("DISCONNECT")) {
    server.sendHeader("Location", "/login");
    server.sendHeader("Cache-Control", "no-cache");
    server.sendHeader("Set-Cookie", "ESPSESSIONID=0");
    server.send(301);
    return;
  }
  if (server.hasArg("USERNAME") && server.hasArg("PASSWORD")) {
    if (server.arg("USERNAME") == WWW_USER &&  server.arg("PASSWORD") == WWW_PASS) {
      server.sendHeader("Location", "/");
      server.sendHeader("Cache-Control", "no-cache");
      server.sendHeader("Set-Cookie", "ESPSESSIONID=1");
      server.send(301);
      return;
    }
    msg = "Wrong username/password! try again.";
  }
  String content = "<html><body><form action='/login' method='POST'>Authenticate to access controls<br>";
  content += "Username:<input type='text' name='USERNAME' placeholder='user name'><br>";
  content += "Password:<input type='password' name='PASSWORD' placeholder='password'><br>";
  content += "<input type='submit' name='SUBMIT' value='Submit'></form>";
  content += msg;
  content += "<br></body></html>";
  server.send(200, "text/html", content);
}

//root page can be accessed only if authentification is ok
void handleRoot() {
  String header;
  if (!is_authenticated()) {
    server.sendHeader("Location", "/login");
    server.sendHeader("Cache-Control", "no-cache");
    server.send(301);
    return;
  }
  String content = "<html><body><form action='/config' method='POST'><H2>Synferno Delay Controls</H2><br>";
  content += "Offset:<select name='OFFSET'>";
  for (int i=0; i<MAX_OFFSET; i++){
    content += "<option value='" + String(i) + "'" + (i == offset ? " selected" : "") + ">" + String(i) + "</option>";
  }
  content += "</select><br>";

  content += "Duration:<select name='DURATION'>";
  for (int i=0; i<MAX_DURATION; i++){ // TODO: get max offset from ino
    content += "<option value='" + String(i) + "'" + (i == duration ? " selected" : "") + ">" + String(i) + "</option>";
  }
  content += "</select><br>";
  
  content += "BPM:<select name='BPM'>";
  for (int i=0; i<MAX_BPM; i++){ // TODO: get max offset from ino
    content += "<option value='" + String(i) + "'" + (i == bpm ? " selected" : "") + ">" + String(i) + "</option>";
  }
  content += "</select><br>";

  content += "Mode:<select name='MODE'>";
  content += "<option value='0'";
  content += (mode == 0 ? " selected" : "");
  content += ">Midi</option>";
  content += "<option value='1'";
  content += (mode == 1 ? " selected" : "");
  content += ">Manual</option>";
  content += "</select><br>";

  content += "<input type='submit' name='SUBMIT' value='Submit'></form><br></body></html>";
  server.send(200, "text/html", content);
}

void handleConfig() {
  if (!is_authenticated()) {
    server.sendHeader("Location", "/login");
    server.sendHeader("Cache-Control", "no-cache");
    server.send(301);
    return;
  }
  if (server.hasArg("OFFSET")) {
    offset = server.arg("OFFSET").toInt();
  }
  if (server.hasArg("DURATION")) {
    duration = server.arg("DURATION").toInt();
  }
  if (server.hasArg("BPM")) {
    bpm = server.arg("BPM").toInt();
  }
  if (server.hasArg("MODE")) {
    mode = server.arg("MODE").toInt();
  }

  Serial.print('O');
  Serial.print(offset);
  Serial.print('\n');
  Serial.print('D');
  Serial.print(duration);
  Serial.print('\n');
  Serial.print('B');
  Serial.print(bpm);
  Serial.print('\n');
  Serial.print('M');
  Serial.print(mode);
  Serial.print('\n');

  server.sendHeader("Location", "/");
  server.send(301);
}

void handleNotFound() {
  String message = "File Not Found\n\n";
  message += "URI: ";
  message += server.uri();
  message += "\nMethod: ";
  message += (server.method() == HTTP_GET) ? "GET" : "POST";
  message += "\nArguments: ";
  message += server.args();
  message += "\n";
  for (uint8_t i = 0; i < server.args(); i++) {
    message += " " + server.argName(i) + ": " + server.arg(i) + "\n";
  }
  server.send(404, "text/plain", message);
}

void setup() {
  Serial.begin(115200);
  while(!Serial);

   // configure soft access point
  WiFi.softAPConfig(IPAddress(LOCAL_IP), IPAddress(GATEWAY), IPAddress(SUBNET));
  // initialize access point
  WiFi.softAP(AP_SSID, AP_PASS);
  // set host name for access point
  MDNS.begin(HOSTNAME);

  // configure webserver endpoints
  server.on("/", handleRoot);
  server.on("/login", handleLogin);
  server.on("/config", handleConfig);
  server.onNotFound(handleNotFound);

  //here the list of headers to be recorded
  const char * headerkeys[] = {"User-Agent", "Cookie"} ;
  size_t headerkeyssize = sizeof(headerkeys) / sizeof(char*);
  //ask server to track these headers
  server.collectHeaders(headerkeys, headerkeyssize);
  server.begin();
}

void loop() {
  // Handle webserver requests
  server.handleClient();

  // Handle serial requests
  while (Serial.available() > 0) {
    int inChar = Serial.read();
    if (isDigit(inChar)) {
      inNum = inNum * 10 + inChar;
    } else if ((char)inChar != '\n') {
      inCommand = (char)inChar;
    }

    if ((char)inChar == '\n') {
      switch (inCommand) {
        case 'O':
          offset = inNum;
          break;
        case 'D':
          duration = inNum;
          break;
        case 'B':
          bpm = inNum;
          break;
        case 'M':
          mode = inNum;
          break;
      }
      inNum = 0;
      inCommand = '\0';
    }
  }
}

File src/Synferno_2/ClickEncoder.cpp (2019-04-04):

#include "ClickEncoder.h"

// ----------------------------------------------------------------------------
// Button configuration (values for 1ms timer service calls)
//
#define ENC_BUTTONINTERVAL    10  // check button every x milliseconds, also debouce time
#define ENC_HOLDTIME        1200  // report held button after 1.2s

// ----------------------------------------------------------------------------

ClickEncoder::ClickEncoder(uint8_t CLK, uint8_t DT, uint8_t BTN, bool active)
  : delta(0), lastClkState(true), lastBtnState(false),
    button(Open),
    pinCLK(CLK), pinDT(DT), pinBTN(BTN), pinsActive(active)
{
  uint8_t configType = (pinsActive == LOW) ? INPUT_PULLUP : INPUT;
  pinMode(pinCLK, configType);
  pinMode(pinDT, configType);
  pinMode(pinBTN, configType);
}

// ----------------------------------------------------------------------------
// call this every 1 millisecond via timer ISR
//
void ClickEncoder::service(void)
{
  unsigned long now = millis();

  bool thisClkState = digitalRead(pinCLK) == pinsActive; // is the data pin active?
  if (thisClkState && !lastClkState) { // did the data pin just become active?
    if (digitalRead(pinDT) == HIGH) {
      delta++;
    } else {
      delta--;
    }
  }
  lastClkState = thisClkState;

  // handle button
  //
#ifndef WITHOUT_BUTTON
  static uint16_t keyDownTicks = 0;
  static unsigned long lastButtonCheck = 0;

  if (pinBTN > 0 // only check button if a pin has been provided
      && (now - lastButtonCheck) >= ENC_BUTTONINTERVAL) // checking button is sufficient every 10-30ms
  { 
    lastButtonCheck = now;
    
    bool thisBtnState = digitalRead(pinBTN) == pinsActive;
    if (thisBtnState) { // button is depressed
      if (thisBtnState == lastBtnState) { // button continues to be held
        keyDownTicks++;
        if (keyDownTicks > (ENC_HOLDTIME / ENC_BUTTONINTERVAL)) {
          button = Held;
        }
      } else { // button has just been pressed
        button = Clicked;
      }
    } else { // key is up
      if (button == Held) {
        button = Released;
      }
      keyDownTicks = 0;
    }
    lastBtnState = thisBtnState;
  }
#endif // WITHOUT_BUTTON

}

// ----------------------------------------------------------------------------

int16_t ClickEncoder::getValue(void)
{
  int16_t val;
  
  cli();

  val = delta;
  delta = 0;

  sei();
  
  return val;
}

// ----------------------------------------------------------------------------

#ifndef WITHOUT_BUTTON
ClickEncoder::Button ClickEncoder::getButton(void)
{
  ClickEncoder::Button ret = button;
  if (button != ClickEncoder::Held) {
    button = ClickEncoder::Open; // reset
  }
  return ret;
}
#endif

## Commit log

2018-11-24 wip frequency button group
2018-11-26 wip frequency button group compiling but throwing panic
2018-12-03 physically wiring and fixing bugs: pin reassignment, I2C oled
    [ButtonGroup.cpp, MIDI.cpp, Solenoid.h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]
2018-12-12 wip: moved OLED to SPI, and moved button inputs to read-only GPIO. starting to replace the 2 POTs with a single rotary encoder.
    [Synferno_2.ino]
2018-12-18 wip: introduced neu-rah/ArduinoMenu library. Configured dummy menu over I2S.
2018-12-25 wip: Moved to Mega and Lolin D1 mini; Prototype wired. Almost all code to be rewritten
2019-01-01 wip: all but Webserver and Tap button written. Does not function correctly (oled non-functional, so hard to tell where the proplem lies).
    [ButtonGroup.cpp, MIDI.cpp]
2019-01-02 wip: Fire buttons fixed. OLED and encoder partially functional.
    [ButtonGroup.cpp, Synferno_2.ino]
2019-01-04 acceptable base functionality on Mega. However, tap button and webserver are non-functional and fast encoder rotations block clock ticks
2019-01-06 replace U8G2 with U8X8 to solve encoder rotation blocking. Change bpm to float with .1 step
    [Synferno_2.ino]
2019-01-16 implemented Tap button.
2019-02-05 fix bugs in manual fire buttons
    [Synferno_2.ino]
2019-02-06 suspend beat reactions (firing and clock LEDs) when zero button is held
2019-02-18 replace blue buttons with yellow; set bpm to default on mode toggle
    [MIDI.cpp, Synferno_2.ino]
2019-02-18 gracefully decay poofers to alternating on few millis per trigger
2019-03-03 implement web server; handle tap and zero buttons consistently; blink beat indicator after delay
2019-03-09 make frequency buttons confirgurable
2019-03-09 component footprint diagram
2019-03-10 create cut holes diagram for major components (no screw holes yet)
2019-03-13 completed placed components diagram, but still need screw holes
2019-03-13 added Buck Converter to diagram
2019-03-22 shifted buttons so that nothing requires glue: MIDI breakout can be bolted on and PSU is held with brackets
    [PSU BRKT.stl, PSU Stop.stl]
2019-04-01 ready to cut. Changed to new button for Fire All; moved button locations.
2019-04-02 rearranged buttons
2019-04-03 moved tap and zero buttons next to display
2019-04-04 successfully implemented new rotary encoder
2019-06-17 misc. Remove placeholder rhythms; remove Suspend feature; dim frequency leds
2019-07-04 led lumosity and readability improvements, and manual bpm set fix
    [Synferno_2.ino]
2019-07-08 wip introduce fire marshal push all fire time determination to it. Currently has but where priority (and available ticks per trigger?) are not correctly set
    [Synferno_2.ino]
2019-07-09 add basic sequences. One bug remains: when BPM or duration is too high, triggers will stop as minimum required ticks tops out
    [Synferno_2.ino]
2019-07-10 allow setting both short and long poofs in sequences
    [Synferno_2.ino]
2019-07-31 priority was set to sequence on menu change, so when changing sequence priority menu label is no longer correct. Now just pass priority at trigger retrieval time
    [Synferno_2.ino]
